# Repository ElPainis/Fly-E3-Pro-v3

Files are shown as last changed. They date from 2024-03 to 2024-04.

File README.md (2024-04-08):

${\small{\textcolor{darkgrey}{\texttt{Release: V1.22}}}}$

# ⚠️⚙️ Sovol SV06/+ Fly-E3-PRO-V3 conversion ⚙️⚠️

This repository contains guide for the hardwareconversion for the Fly-E3-PRO-V3 & Klipper firmware for the **Sovol SV06** 3D printer. I made this as a branch in collaboration with Bassamantor archive a better accessibility for the whole community. The hardware conversion described here should fit the SV06+ but is untested yet. Guide and Klipper Config for the is WIP SV06+. Alos check out [Bassamanators](https://github.com/bassamanator/Sovol-SV06-firmware/tree/master) GitHub.

| Printer | Branch |
| --- | --- |
| ${\normalsize{\textcolor{darkturquoise}{\texttt{Sovol SV06 Fly-E3-V3-Pro}}}}$ | ⚡ ${\small{\textcolor{darkturquoise}{\texttt{YOU ARE HERE}}}}$ ⚡ |
| Sovol SV06 | [master](https://github.com/bassamanator/Sovol-SV06-firmware/tree/master) |
| Sovol SV06 Skr-Mini-E3-V3.0 | [skr-mini-e3-v3](https://github.com/bassamanator/Sovol-SV06-firmware/tree/skr-mini-e3-v3) |
| Sovol SV06 Plus | [sv06-plus](https://github.com/bassamanator/Sovol-SV06-firmware/tree/sv06-plus) |
| All other printers | [any-printer](https://github.com/bassamanator/Sovol-SV06-firmware/tree/any-printer) |

**A short preview about what can you expect:**

(not realtime, speedup for better overview)



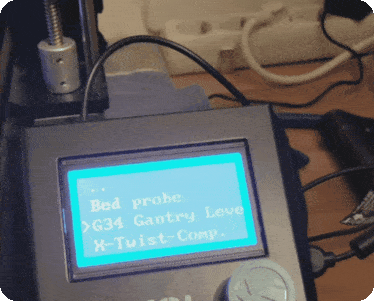
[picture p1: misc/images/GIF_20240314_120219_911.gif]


I am creating these files for my personal use and cannot be held responsible for what it might do to your printer. Use at your own risk.

## Outline
- [Contribution](#contribution)
- [Preface](#preface)
- [Disclaimer](#Disclaimer)
- [Features](#features)
- [Stay Up-to-Date](#stay-up-to-date)
- [Hardware Conversion](#Hardware-Conversion)
  - [BOM](#BOM)
  - [Step 1 - Electrical wiring](#Step-1---Electrical-wiring)
  - [Step 2 - Disassemble the mobo-box and ribbon-cable](#Step-2---Disassemble-the-mobo-box-and-ribbon-cable)
  - [Step 3 - Modifing Extruder Ribbon-Cable](#Step-3---Modifing-Extruder-ribbon-Cable)
  - [Step 4 - Modifing Mobo enclosure](#Step-4---Modifing-Mobo-enclosure)
  - [Step 5 - Stepper wiring](#Step-5---stepper-wiring)
  - [Step 6 - Assembly](#Step-6---assembly)
  - [Step 7 - Optional Neopixel](#Step-7---Optional-Neopixel)
  - [Hardware conversion sources](#hardware-conversion-sources)
- [Klipper Installation](#klipper-installation)
  - [Before You Begin](#before-you-begin)
  - [Flash Firmware](#flash-firmware)
  - [Download OSS Klipper Configuration](#download-oss-klipper-configuration)
- [Initial Steps](#initial-steps)
  1. [Adjust Configuration with MCU Path](#adjust-configuration-with-mcu-path)
  2. [Configure Your Printer](#configure-your-printer)
- [Adjust Your Slicer](#adjust-your-slicer)
- [Support Me](#support-me)
- [Directory Structure](#directory-structure)
- [FAQ](#faq)
- [Useful Resources](#useful-resources)
- [Sovol Official Links](#sovol-official-links)
- [Sources](#sources)

## Contribution
:heart:I want to thank [Bassamanator](https://github.com/bassamanator/Sovol-SV06-firmware/tree/sv06) for sharing his Klipper-Config and giving me advice for the whole project. Further I thank [Jan Oerter](https://www.youtube.com/user/MegaMuelleimer/) and [Dominik Schmidt](https://www.youtube.com/@dr.klipper) for their Anycubic i3 Mega conversion that inspired me for this project. Please check out [their GitHub](https://github.com/Schmelzerboy/I3-Mega-Klipper&ved=2ahUKEwj_2fKx-8qEAxW__7sIHc9iDd8QFnoECBUQAQ&usg=AOvVaw2BVSSPE56Auy_gCTLLL8iX) as well. Last but not least I thank the big maker community for advice, troubleshooting and sharing awesome creations. Beeing part of a community give us a feeling of wholesome and connected. Without you and the regardless help this project wouldnt be possible. Youre breathtaking! :heart:

## Preface

This Mod includes minor manipulation of the provided hardware. If this mod doesnt work out for you, its reversable in majority. You have to live with some minor cosmetic changes of the mainboard enclosure.

Preassumtion is you have crimping and solder tools and know how to use them. Many helpful sources are provided here like :tv:**vidoes** :tv: and 🖼️**pictures**🖼️ to make the job easier. Keep in mind youre the only one that can be hold responsible if things go wrong.

Requirements:
- screw drivers
- soldering iron & flux
- crimptool for insulated Terminals
- shrink Tubes
- dupon Connectors
- heatgun
- pliers to cut and to Grab
- wire stripper
- helping hand
- small file(s)
- zipties

Everything in this guide aims for easy accessibility. Despite it the prerequisite for this guide is youre familiar with Klipper. This conversion is recommend advanced users which are familiar with handling electronics and used Klipper at least once before.

> [!CAUTION]
> ## DISCLAIMER:
> 🔥⚡💀⚡🔥
>
> The conversion needs modification of the PSU wiring. This contains the potential risk of damaging your machine, firehazard or worst threading your life. If you unshure how to do proceed stop right away and get help! Don't improvise at something that can potentialy threading your life when done improper! When turning on the machine first time after conversion I recommend having a fire extinguisher to hand for the worst case. If issues occoure leave feedback by opening an issue. Read the complete guide with full attention. I can not be hold accountable for any damage or injuries. Youre doing this at your own risk.
> 
> 🚨 some basic safety rules for electrical DIY 🚨:
> 1. Turn Off the machine and unplug the Power
> 2. Make shure it cant be plugged in or turned on again accidantial.
> 3. Don't be lazy but smart. Unplug and disassemble the parts you want to modify as far as possible to get them on a table.
> 4. Use proper tools.

## Features
- Harware:
  - Z-Tilt & Gantry Level to further improve parallel alignment to printbed.
  - silent Hotend-Fan while printer is idling. Optional PWM!
  - dedicated driver cooling fan. Optional PWM!
  - Optional: Neopixel with preconfigured effects for your printhead for better view and status feedback. 🔴🟢🔵 Full customization via `neopixel.cfg`
     - This Mod requieres a already installed mod for partcooling! Like [these](https://www.printables.com/de/model/685826-high-flow-ducts-for-sv06-single-and-double-5015-pa)
- Klipper:
   - This is basically provided by awesome Bassamanator. I only did minor changes to the `printer.cgf` to make it work with the Fly E3 Pro V3. Only the greatest masters are getting copyied, so credit goes to Bassamanator!
   - 💥 This Klipper configuration is an _endpoint_, meaning that it contains **everything** that you could possibly need in order to have an excellent Klipper experience! 💥
   - Minimum configuration settings for `Mainsail` and `Fluidd`.
   - Macros:
     - **Improved** mechanical gantry calibration/`G34` macro that provides the user audio feedback, and time to check the calibration.
     - Misc macros: `PRINT_START`, `CANCEL_PRINT`, `PRINT_END`, `PAUSE`, `RESUME`.
     - Parking macros (parks the printhead at various locations): `PARKFRONT`, `PARKFRONTLOW`, `PARKREAR`, `PARKCENTER`, `PARKBED`.
     - Load/unload filament macros.
     - `PURGE_LINE` macro.
     - `TEST_SPEED` macro. Find instructions [here](#how-do-i-use-the-test_speed-macro).
     - Custom Diplay Menu
     - Klipper Adaptive Meshing & Purging (KAMP) integrated. Read about it [here](#how-do-i-enable-kamp-klipper-adaptive-meshing--purging).

[🔼 Back to top](#outline)

## Stay Up-to-Date

${\normalsize{\textcolor{goldenrod}{\texttt{Star ⭐ this project.}}}}$

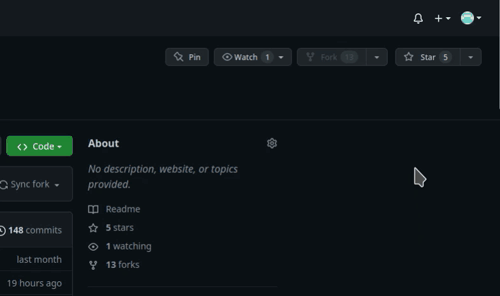
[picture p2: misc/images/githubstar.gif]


Watch for [updates]

[🔼 Back to top](#outline)

## Hardware Conversion
## BOM

This BOM is meant to give you an overview and some recommendation what is needed. Some parts are essential,  some can be done by DIY. Some there are a few parts with prequesitions. I marked them with the following pattern:
- basic requirement: :heavy_check_mark:
- can be done by DIY: ⚙️
- has prequesition: :large_blue_diamond:
- not necessary for the conversion, optional: :small_orange_diamond:

> [!CAUTION]
> ⚡ If you like to improvise: Dont improvise on the wiring. Use at least a diameter of AWG14 or 2,0mm². Thinner cables lead to a non reliable voltage supply for to mobo with may unexpected behavior or worse. ⚡

| Essential | Needed for Step  | Part Name | Price | Source |
| ----- | ----- | ---- | ----- | --- |
| :heavy_check_mark: | (6) Assembly  | Fly-E3-Pro-V3 | ~40 Money  | [AliExpress](https://a.aliexpress.com/_EwY8p5L) |
| :heavy_check_mark: | (1) Electrical wiring | 200cm each AWG14 Red & Black  | ~4 Money  | [AliExpress](https://a.aliexpress.com/_ExgydLn)  |
| :heavy_check_mark: | (1) Electrical wiring  | Cable Lug 3xSV2-4 & 3xSV2-5 | ~5 Money  | [AliExpress](https://a.aliexpress.com/_Exw61D7)  |
| :heavy_check_mark: | (1) Electrical wiring | MR60 Connector | ~6 Money  | [AliExpress](https://a.aliexpress.com/_EzVy9PX)  |
| :heavy_check_mark: | (1) Electrical wiring | Wire sleeve (8mm ID) | ~1 Money  | [AliExpress](https://a.aliexpress.com/_EJrBNvF)  |
| :heavy_check_mark: | (1) Electrical wiring  | Zipties 3.6mm width | ~2 Money  | [AliExpress](https://de.aliexpress.com/item/1005004666948984.html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)  |
| :heavy_check_mark: | (1) Electrical wiring | Zipties 2.5mm width | ~2 Money  | [AliExpress](https://de.aliexpress.com/item/1005004666948984.html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)  |
| :small_orange_diamond: | (3) Modifing Extruder Ribbon-Cable | Mainboard Ribbon Cable | ~ 12 Money | [Sovol](https://www.sovol3d.com/products/sovol-sv06-adapter-board-pcb-breakout-module-adapter-board-mainboard-ribbon-cable)|
| ⚙️ | (3) Modifing Extruder Ribbon-Cable | 2x JST XH 2,54 2pins | ~ 1 Money | [AliExpress](https://de.aliexpress.com/item/32954418743.html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)|
| ⚙️ | (3) Modifing Extruder Ribbon-Cable | 1x 5pin Female Dupont with wires | ~ 3 Money | [AliExpress](https://de.aliexpress.com/item/1005003638697583.html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)|
| :small_orange_diamond: | (3) Modifing Extruder Ribbon-Cable | Alternative to Dupont wires | ~ 20 Money | [Local Amazon](https://www.amazon.de/dp/B0CLD7S5VC/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)|
| ⚙️ |(6) Assembly| 50cm Stepper Wire | ~1 Money |[AliExpress]( https://a.aliexpress.com/_EHGpQVX) |
| ⚙️ |(6) Assembly| 80cm Stepper Wire | ~1 Money |[AliExpress]( https://a.aliexpress.com/_EHGpQVX) |
| :large_blue_diamond: :small_orange_diamond: |(7) Optional Neopixel| 4*1 Bit Neopixel | ~5 Money |[AliExpress](https://de.aliexpress.com/item/32962174474.html) |
| ⚙️ :large_blue_diamond: :small_orange_diamond: | (7) Optional Neopixel | 1x JST XH 2,54 3pins | ~ 1 Money | [AliExpress](https://de.aliexpress.com/item/32954418743.html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)|
| :heavy_check_mark: |Motivation| At least seven cookies or bits of sweets and a cup of hot drink 🍪🍬 | Depents on your taste |Anywhere |

## Step 1 - Electrical wiring
Requirements:
- AWG 14 wires
- MR60 Connector
- cable Lugs
- pliers
- wirestripper
- soldering iron
- crimping tool

> [!NOTE]
> This is the Part for the PSU-wiring to MOBO. You need to cut the wires and the sleeve in lenght, solder it with the connector and crimp the cable lugs.
> You may find this :tv:[video](https://youtu.be/w0pMjZ-rFQA?si=jAx5m2BBQhHhFl7G):tv: helpful for soldering and this :tv:[additional video](https://www.youtube.com/watch?v=GrwDEiFtXIc):tv: for applying the sleeve.

Procedure:
1. Use the pliers to cut the the materials in the length provided by this table:

| Quantity | Color  | Lenght | Needed for | 
| ----- | ----- | ---- | ----- |
| 2x | Red wire | 510 +/-10mm | connector to mobo |
| 1x | Black wire | 510 +/-10mm | connector to mobo |
| 2x | Red wire | 150 +/-5mm | PSU to connector |
| 1x | Black wire | 150 +/-5mm | PSU to connector |
| 1x | Protective sleeve | 470 +/-10mm | connector to mobo |
| 1x | Protective sleeve | 100 +/-10mm | PSU to connector |

> [!NOTE]
> The longer cables will be called CTM (connector to mobo), the short cables PSUC (PSU to connector) mind the 🖼️[electrical wiring diagram](#electrical-wiring-diagram)🖼️ to get an image of what you're about to archive.

2. Solder PSUC

Strip one end and solder all three 150mm wires it into the male connector. Use the helping hand to hold it in place. Round is for ground. A proper electrical connection is crucial as this connector is very likley to heat up and melt when there is a bad solderjoint. Apply the click-on insulation after inspecting the solder joint.

3. Solder CTM

Repeat the process with the three 510mm wires. Use the female connector.

4. Apply sleeve

Apply the sleeve to both wires and add a heatshrink to secure the sleeve and wires in place.

5. Crimping PSUC

Strip 6mm on the one end left and crimp the SV2-5(Bigger Fork) on all three cables. 

6. Crimping CTM

Repeat the process on the 510mm wires mentioned at 5. Use the SV2-4(smaller Fork)this time.

The result should look like this:
### Electrical wireing diagram
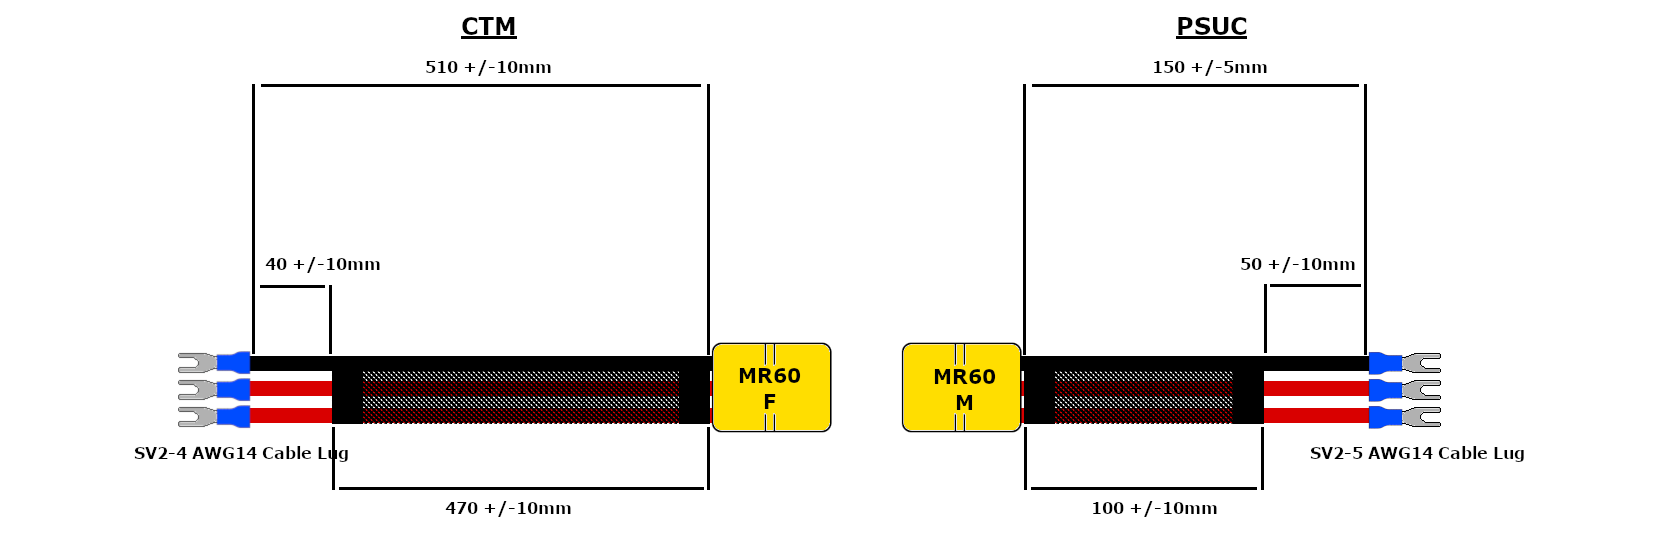
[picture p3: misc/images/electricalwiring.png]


🍪🍬 DONE. Time for a cup of hot drink and a cookie or a sweet. 🍪🍬

[🔼 Back to top](#outline)
## Step 2 - Disassembly

Requirements:
- Pliers
- screwdriver with hexhead

> [!NOTE]
> In this step all electronical parts are gonna disassembled from the printers frame as preparation for following modifications. The motherboard enclosure, stepper cables, ribbon-cable and the motherboard from the enclosure.
> You will may find this :tv:[video](https://www.youtube.com/live/SQ4Nzgl77F8?si=rxNRZa5gnDLFytx2&t=866):tv: till timestamp 22:05 useful. Mind the 🖼️[Sovol SV06 Pinout](#sovol-sv06-pinout)🖼️.

Procedure:
1. Turn off the machine and unplug power!
2. open the enclosure.
3. unscrew the power supply terminals.
4. unscrew the hot bed terminals. 
5. unplug the hot bed thermistor.
6. unplug all stepper motor cables.
7. unplug 'touch screen'
8. cut and remove the zipties in the two bottom outlets that hold the cables **be careful not to cut a wire accidently.**
9. gently remove all wires from the bottom outlets.
    1. Stepper motor cables
    2. Hot bed
10. unplug the ribbon-cable from the extruder-pcb
    1. unplug Nozzle thermistor.
    2. unscrew the nozzle 24V terminals.
    3. unscrew the normal fan 24V terminals.
    4. unplug the controllable fan.
11. close the enclosure and hold it closed. Then unlock mobo-enclosure and remove the enclosure with the ribbon cable from the printers frame.
12. place the motherboard enclosure on a flat surface and open it again to proceed. 
13. cut the ziptie that hold the extruder-ribbon-cable, **Carefully again not to cut a wire accidently.**
14. disassemble the ribbon-cable from the mobo and the enclosure.
15. unscrew the four motherboard screws. Store the motherboard somewhere. If your conversion is successful you wount need it anymore. Keep the screws!
15. back to the printer the Y-motor-cable and dual-Z-motor-cable are taped together. Gently peel of the tape so they're seperated after.
16. remove the Dual-Z-stepper-cable and store it somewhere. If the conversion is sucessful you wount need it anymore.

### Sovol SV06 Pinout


🍪🍬 DONE. Time for a cup of hot drink and a cookie or a sweet. 🍪🍬

[🔼 Back to top](#outline)

## Step 3 - Modifing Extruder Ribbon-Cable

Requirements:
- Wirestripper
- Soldering iron
- flux
- helping hand
- multimeter
- pliers
- tape for marking

> [!NOTE]
> Modification of the toolhead ribbon cable is neccessary so it fits all the connectors on the Fly-E3-V3-Pro. 🖼️[Schematic 1](#schematic-1)🖼️ down below shows the original toolhead ribbon cable. 🖼️[Schematic 2](#schematic-2)🖼️ shows the final product after modification.

> [!TIP]
> If you having the spare toolhead laying around go and get it. It will be very helpful for this step. A spare toolhead pcb comes really handy as you can easily check if your wiring is as intended.

### schematic 1:


(click for lager picture)

### schematic 2:
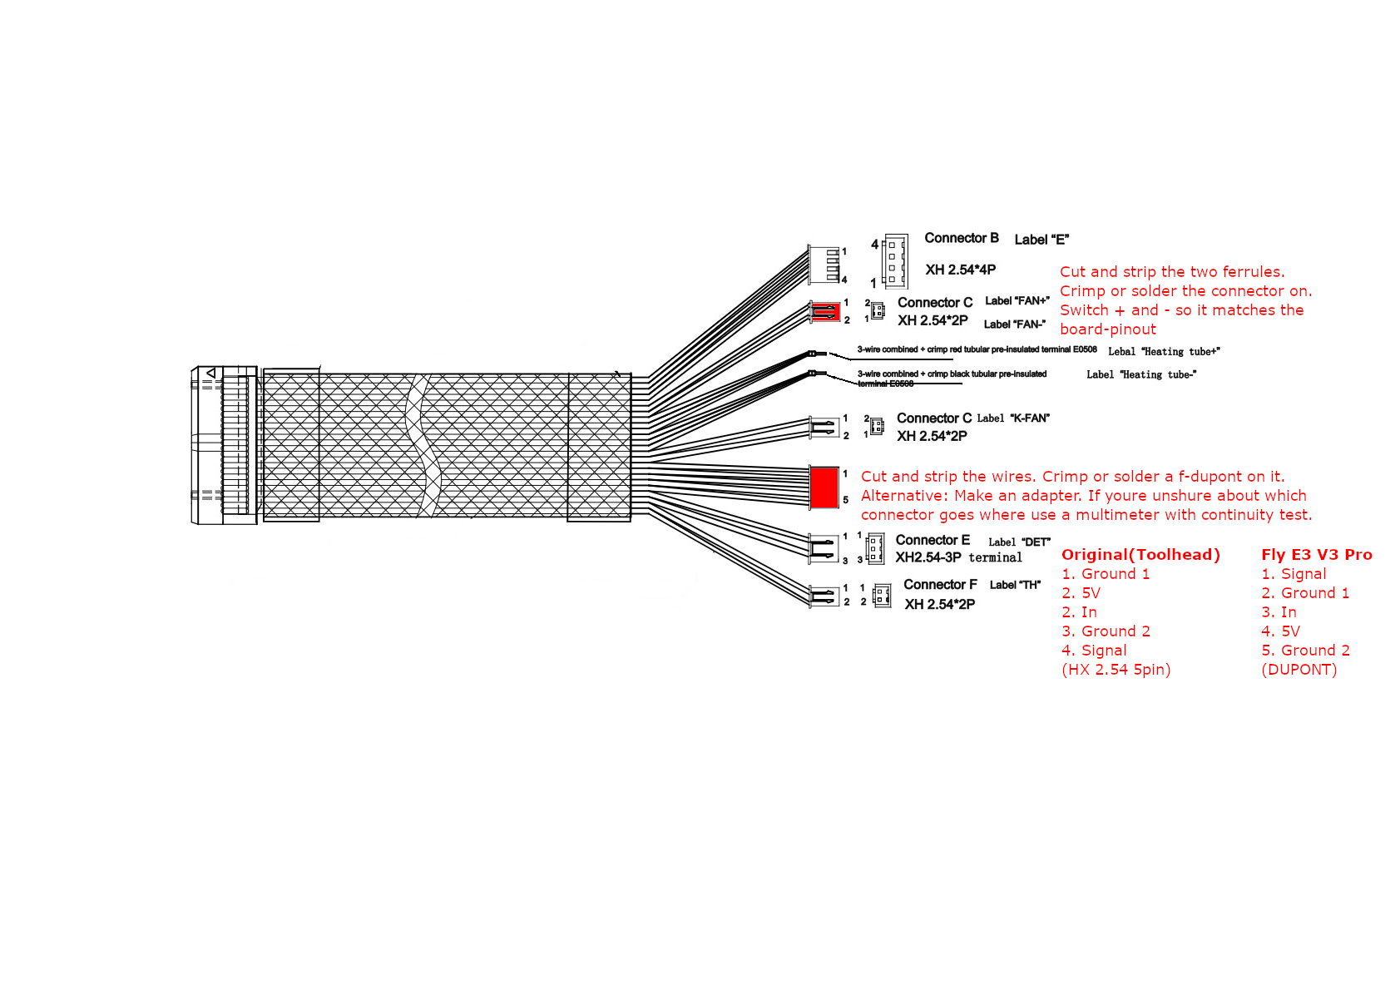
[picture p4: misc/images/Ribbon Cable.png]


(click for lager picture)

Procedure:
1. mark the cables for the probe with a tape so its easier to convert it. Mind the 🖼️[probe cable pinout](#probe-cable-pinout)🖼️.
2. cut the probe connector behind your marks cables and strip ~3mm.
3. cut the fan-ferrules from fan+ and fan- and strip ~3mm.
4. crimp or solder on the Dupont connector on the stripped probe-cables. Mind the 🖼️[probe cable pinout](#probe-cable-pinout)🖼️.
5. crimp or solder on JST-Connector on the stripped fan-cables.
6. check the polarity of the FAN. Mind the 🖼️[board pinout](#board-pinout)🖼️.
7. check the polarity of the K-FAN. Mind the 🖼️[board pinout](#board-pinout)🖼️.
8. check the pinout of the new probe-dupont-connector if it matches the Fly-E3-V3-pro. Mind the 🖼️[board pinout](#board-pinout)🖼️.
9. switch port 1 and 3 of the DET-Connector using the pliers.
10. (Optional) remove the tape marks from the probe-connector.

> [!TIP]
> Its possible to leave out the soldering or crimping job with the probe connetor by getting one of [these](https://www.amazon.de/dp/B0CLD7S5VC/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) and make an adapter. Its not really necessary and more costly, but maybe this is a more convinient option for you.

### Probe cable pinout

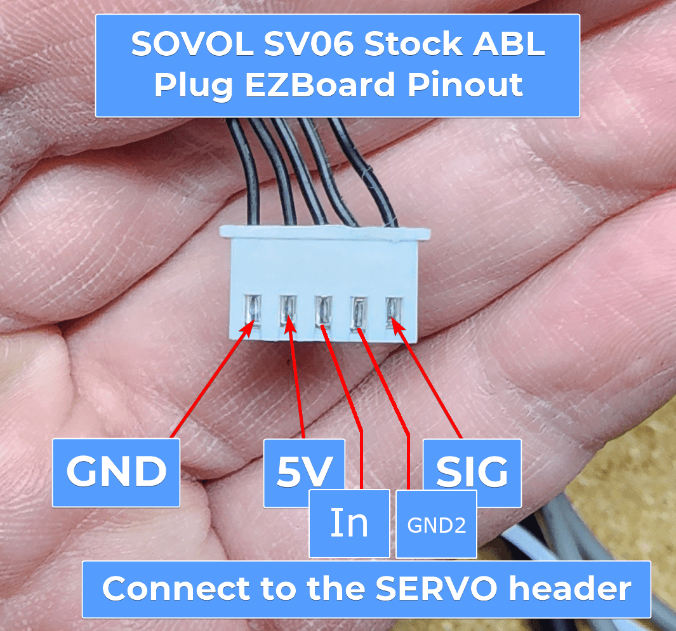
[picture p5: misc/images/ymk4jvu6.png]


### Board pinout
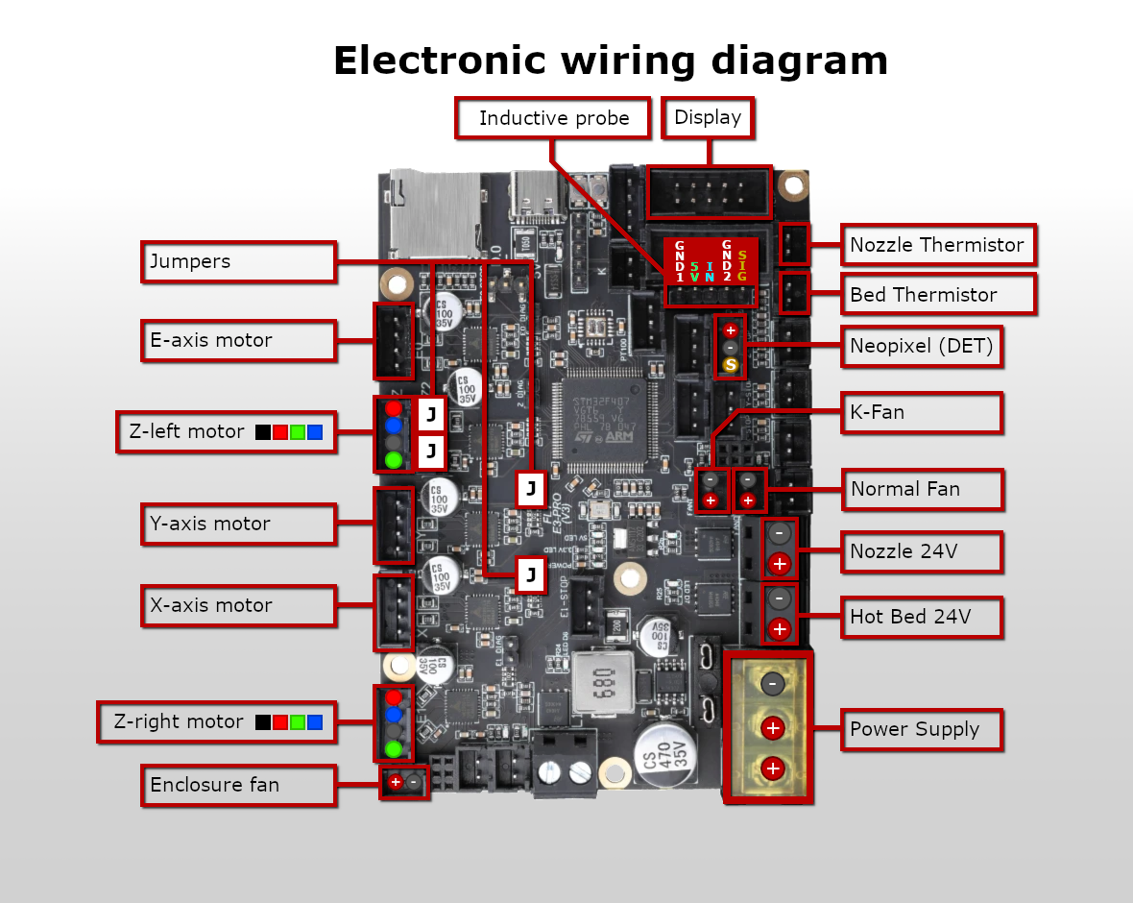
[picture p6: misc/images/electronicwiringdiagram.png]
 

> [!CAUTION]
> I strongly recommend to check wiring with the multimeter and the toolhead pcb if everything is wired up correctly before calling this done.

🍪🍬 DONE. Time for a cup of hot drink and a cookie or a sweet. 🍪🍬

[🔼 Back to top](#outline)

## Step 4 - Modifing Mobo enclosure
Requirements:
- pliers
- small file - For myself I did it with a nail file
- paper towels

> [!NOTE]
> The moobo-enclosure needs minor modification so it fits the Fly-E3-V3-Pro. Mind the 🖼️[enclosure sanding visualization](#enclosure-sanding-visualization)🖼️.

Procedure:
1. Cut the ribs with the pliers marked red in the picture. We need to do that to make room for the Wifi-Antenna at the backside of the board.
2. Sand the holes with the file ~1 up 2mm wider so the USB-connector and SD-Card-slot fit of the Fly-Mobo fit.
3. Test if the Fly mobo fits into the enclosure. If not check for for connectors especially the SD-slot as it stand out alot. A few tries may required to get it right.
4. When the board fits nice and snuggely into the enclosure remove it again clean the enclosure with water and dry it with paper towels.

### Enclosure sanding visualization
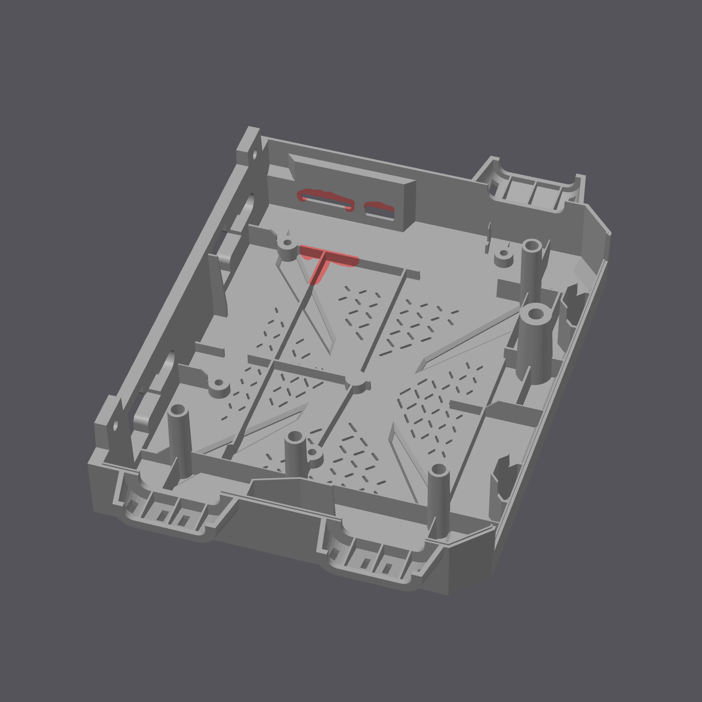
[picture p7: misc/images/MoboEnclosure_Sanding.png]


🍪🍬 DONE. Time for a cup of hot drink and a cookie or a sweet. 🍪🍬

[🔼 Back to top](#outline)

## Step 5 - Stepper wiring
Requirements:
- pliers

> [!NOTE]
> The two new stepper motor cables need modification for correct wiring.

Procedure:
1. check the 4-pin-connector for orientation for both Z motor cables on the Fly-E3-Pro-V3. Mind the [Z-Motor cable chart](#z-motor-cable-chart).
2. use the pliers to remoove the pins on the motherboard connector. You can pinch on the pins with moderate force, they wount break. Bend the little nose up again befor inserting them back in their connector-housing. Mind the left sequence shown in the table below.
3. check the 6-pin connector for orientation of both cables on Z-steppers.
4. use the pliers to get the right orientation on stepper connector. Bend the little plastic-holders gently upwarts and remove the pins. **Dont try to push the pins, you will break them!**. Bend the nose back again before inserting them in their connector-housing. Mind the right sequence shown in the table below.

### Z-Motor cable chart
| ⚪ Motherboard (up to down)  | ⬜ Stepper (left to right) | 
| ----- | ---- |
| 🔴 | ⬛🟥🟩🟦 |
| 🔵 | |
| ⚫ | |
| 🟢 | |

The result should look like this after final assembly:

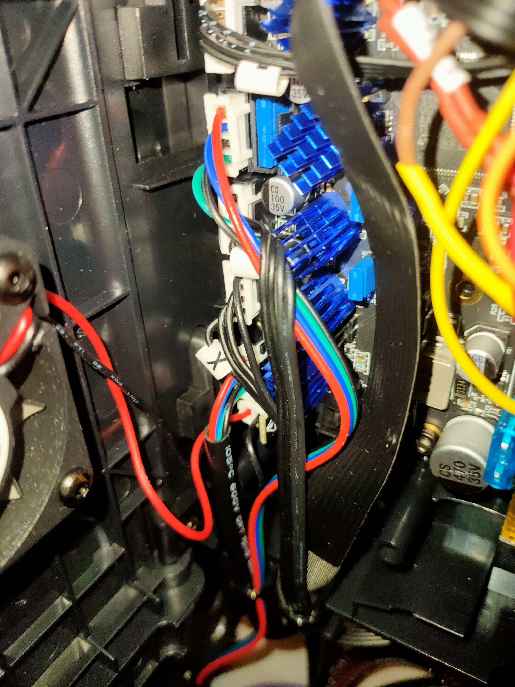
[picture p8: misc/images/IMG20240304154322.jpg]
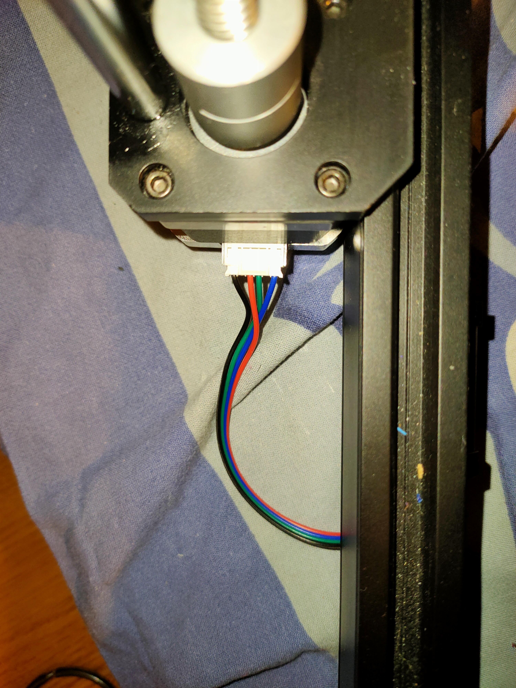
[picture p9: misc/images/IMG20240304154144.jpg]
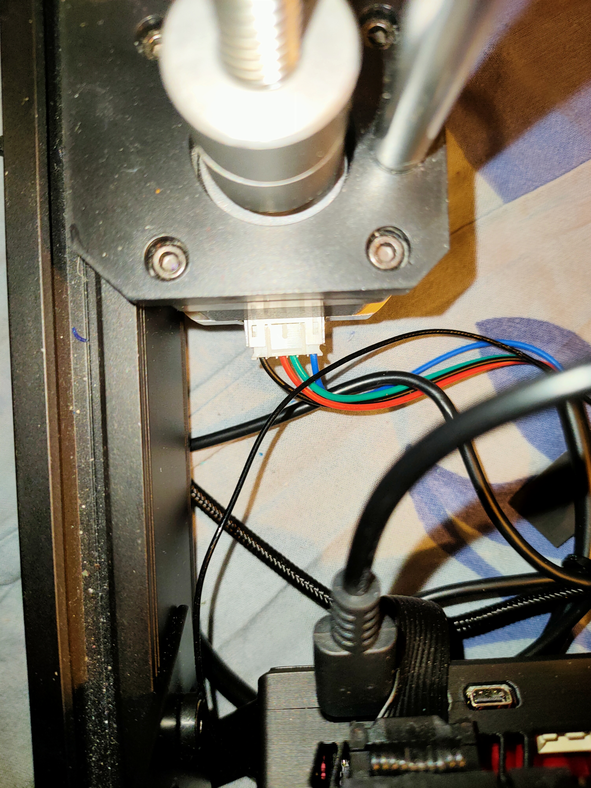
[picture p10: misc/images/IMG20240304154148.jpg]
  

🍪🍬 DONE. Time for a cup of hot drink and a cookie or a sweet. 🍪🍬

[🔼 Back to top](#outline)

## Step 6 - Assembly
Requirements:
- pliers
- zipties
- screwdriver with hex-head

> [!NOTE]
> Put everything together in reverse oder of dissasembly and check if the board is turning on after.

Procedure:
1. placing the motherboard
   1. place the jumpers and the fuse on the Fly-E3-V3-Pro if you havent already.
   2. place the heatsinks on all drivers.
   3. get the Fly-E3-V3-Pro and screw it into the motherboard enclosure using the four screws we saved from the disassembly.
2. electrical wiring 🖼️[mind the electronic wiring diagram](#electronic-wiring-diagram)🖼️
   1. get the cable we prepared earlier at [Step1](#Step-1---Electrical-wiring) and screw down the the lug connectors in the board. Terminal 3 is for ground. The other two are for voltage.
   2. Route the Power power cable we just screw in down in the opening. Dont ziptie yet!
3. Install ribbon cable 🖼️[mind the electronic wiring diagram](#electronic-wiring-diagram)🖼️
   1. get the modified ribbon cable and place it in the upper opening of the enclosure. Secure it with a ziptie.
   2. plug in all the cables from the extruder ribbon cable.

>[!IMPORTANT]
> Mind the orientation of the modified sensor-dupont-connector! Mind the wiring diagram down below to get everything right. Close it after with the screw.

4. assemble enclosure
   1. place the enclosure at the printers-frame and lock it in place.
   2. screw in the bed power cables and the thermistor.
   3. Route the power cable in place. Its much more stiff now so its now bigger bend radius as we crossing your bed-cable. Dont worry it isnt an issue. Secure the two cables with a ziptie.

>[!IMPORTANT]
> Mind the picture below to get an idea what is mentioned here.

5. stepper wiring 🖼️[mind the electronic wiring diagram](#electronic-wiring-diagram)🖼️
   1. plug in the 20cm stepper motor cable at Z.
   2. plug in the Y stepper motor cable at Y.
   3. plug in the X stepper motor cable at X.
   4. plug in the 80cm stepper motor cable at E1 for the right stepper.
   5. route all the cables through the hole and secure them with a ziptie.

>[!IMPORTANT]
> test if the motherboard-enclosure is closing properly. If not check for conflicts with the cables. **DONT TRY TO FORCE IT CLOSE, IT WILL BREAK!**

6. frame cable routing. Mind the 🖼️[frame visualization](#frame-visualization) for substep i till vii 🖼️ and the Mind the [Z-Motor cable chart](#z-motor-cable-chart) for substep iii and viii.
   1. route the Y-stepper cable, the 80 cm stepper-motor-cable and the power cable underneath the Y-stepper. Secure them with a ziptie.
   2. route the 20cm stepper motor cable underneath the left 2040 extrusion. Remove the plastic cover. Route the cable inside the left extrusion and click in the cover over back on to secure it.
   3. plug the 20cm stepper motor cable into the left stepper motor.
   4. Remove the plastic extrusion cover under the right 2040 extrusion.
   5. lift the frame at the right back corner and losen the glued foot on the right back corner by twisting it with moderate force. Do not remove completly!
   6. route the 80cm stepper motor underneath the foot and press it back on. 
   7. route the 80cm cable further to the motor and click in the plastic cover to secure it.
   8. Plug the cable into the right motor.

>[!IMPORTANT]
> check if everything is well routed. Move the bed slowly back and forth and sense if there is any resistance. Also check for any other potential collisions with the rerouted cables. If everything seems well proceed. If not check the uncutted zipties if theyre the source of the issues.

7. PSU wiring
> [!NOTE] 
> You may find this :tv:[video](https://youtu.be/YTUfaLn1awc?si=KQ4-fF_gmnzqi0rD&t=149):tv: till timestamp 3:47 helpful

   1. disassemble the psu by release the two M4 bolts from the frame. 
   2. disassemble the PSU-cover from PSU.
   3. release the two screws in the PSU terminal holding the the cable lugs.
   4. remove the whole now loose cable with the connector.
   5. screw in the short cable you made at step 1. Mind the polarity on the PSU. **Double check a mistake May fry your board!** 🖼️[Mind the electronic wiring diagram](#electronic-wiring-diagram)🖼️.
   6. assembple back psu-cover and route the cable with connector trough the hole provided by the cover.
   7. screw the psu back on the printers frame.
8. Final steps
   1. connect the MR60-connector so the board is provided with power.
   2. check if the psu is turned off and then plug in the power supply.
   3. turn on the power supply. **🔥🧯 A fire extinguisher nearby is recommend. 🧯🔥**
   4. Check if the boards led's and the led of the probe lights up. When nothing is 💥burning/exploding🔥 or smell♨️ weird after 1 minute then everything seems to be fine.
   5. Cut all installed zipties so they dont infere with anything. Mind the 🖼️[frame visualization](#frame-visualization).
   6. close the mainboard enclosure and secure it with the screw.

### electronic wiring diagram


### frame visualization
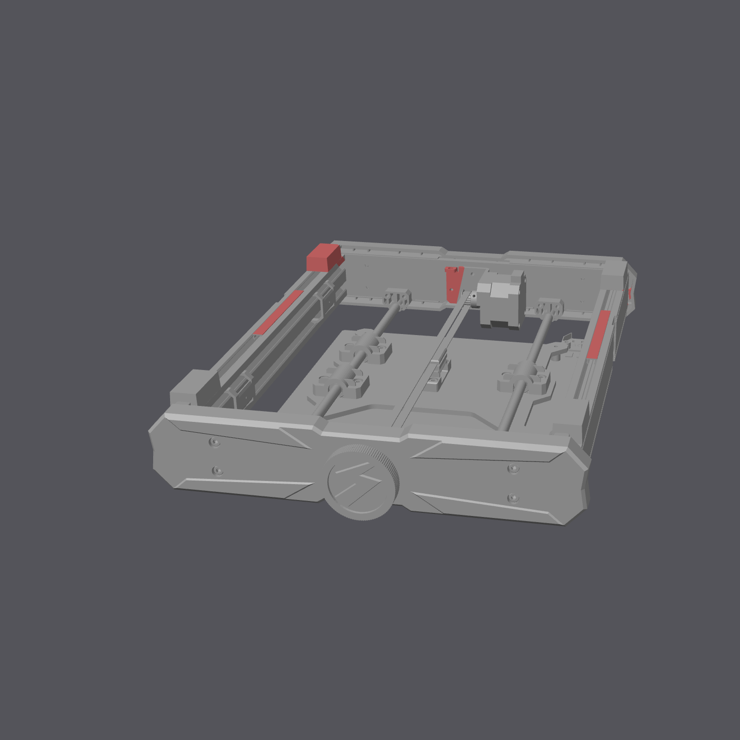
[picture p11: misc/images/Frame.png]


🥳 Congrats your conversion seems to be successfull at this point 🥳
🍪🍬 DONE. Time for a cup of hot drink and a bunch of cookies or sweets. 🍪🍬

[🔼 Back to top](#outline)

##  Step 7 - Optional Neopixel
Requirements:
- printed LED-holder (STL is in Folder 'misc/STL')
- helping Hand
- flux
- Solder iron
- 4*1 Bit Neopixel
- Superglue
- 1x JST XH 2,54 3pins with (pre)crimped connectors and 115 +/- 5mm AWG28 wire
- wirestripper
- pliers
- Two M3*6 screws (its possible to use the ones that holded the original partcooler)

> [!NOTE]
> We are going to solder the wires in the Mini-Neopixel, glue it on the holder and then install it.

> [!IMPORTANT]
> to fullfil this step soldering skills beyond beginners level are required. It's assumed you had practiced at least a few times soldering and did simple solderjobs on PCB's.

 Print Settings:
 - 0.4 Nozzle
 - 0.1mm layerheight
- Solid infill
- Heat resistant material like PETG or ABS
- Place on Buildplate as in the STL

1. Preperation
   1. strip around 2mm of the three AWG 28 wires connected to the JST-header. 
   2. place the Neopixel in the helping hand, clamp it down.
2. Soldering
   1. apply flux on the three pads on the backside and apply tin on the pads with the soldering iron. Go short and hot around 400°C. Very little is enough.
   2. place the prepared cables with the connector over the three soldered pads. Take your time to bring them in position. Clamp them with the helping hand very close over the pads. Its a little fiddly but you make it!
   4. When the cables are in position apply some flux again over the cables and solder them on the pretinned pads. I recommend starting with DIN and work your way to GND. ***Go in very short and hot or may the insulation will start to melt.** 🟡=In 🔴=5V ⚫=GND
   6. check for shorts. If everything seems fine lay it nearby and proceed.
3. Installation on holder
   1. route the cables in the grove with the pliers and gently press the PCB down till everything fits. Its a fiddly job again. If there is alot resistance when pressing the PCB down lift it again and route the cables with the pliers. When everything is right the PCB should go in with a slight click.
   3. Inspect if the pcb sits firmly in the LED-Bracket. When everything seems good, lift it again and apply a drop of superglue on the left and right side of the Neopixel-PCB. Press it on with moderate force for 30 seconds and let it set for ~2 hours.
   4. While the glue is setting you can route the cables through the routing-groove using the pliers.
   5. when the glue is settled screw the holder into the two provided holes for the former partcooler and connect the neopixel to the printhead PCB. Mind the correct wiring, switch if necessary using the pliers to lift the small platic noses. I the cable is a little too long you can route it behind the PCB and then plug the connector in. Mind the 🖼️[Hotend PCB pinout @ P7](#Hotend-PCB-pinout) so your JST-connector should go  🔴=V ⚫=G 🟡=S
   6. secure the cable with a small ziptie on the probes cable so it cant touch the heater block.
4. Testing
   1. See 8 at [setup Klipper](#Configure-Your-printer-and-initial-setup).

The result should look like:

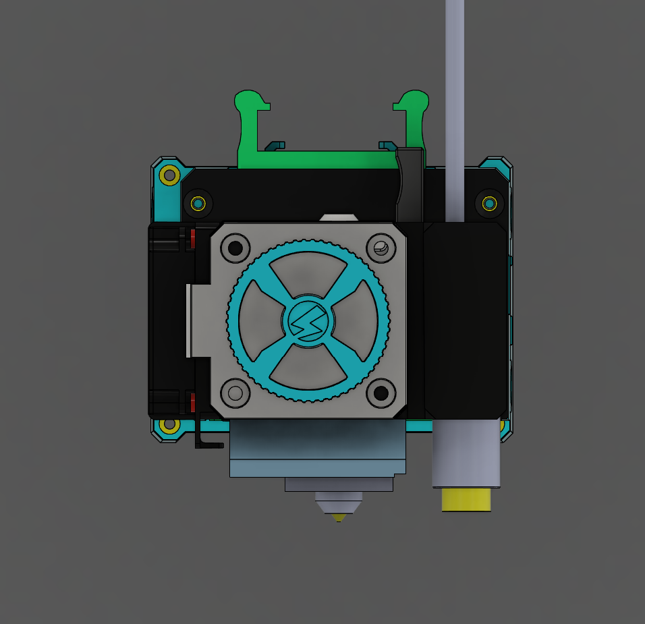
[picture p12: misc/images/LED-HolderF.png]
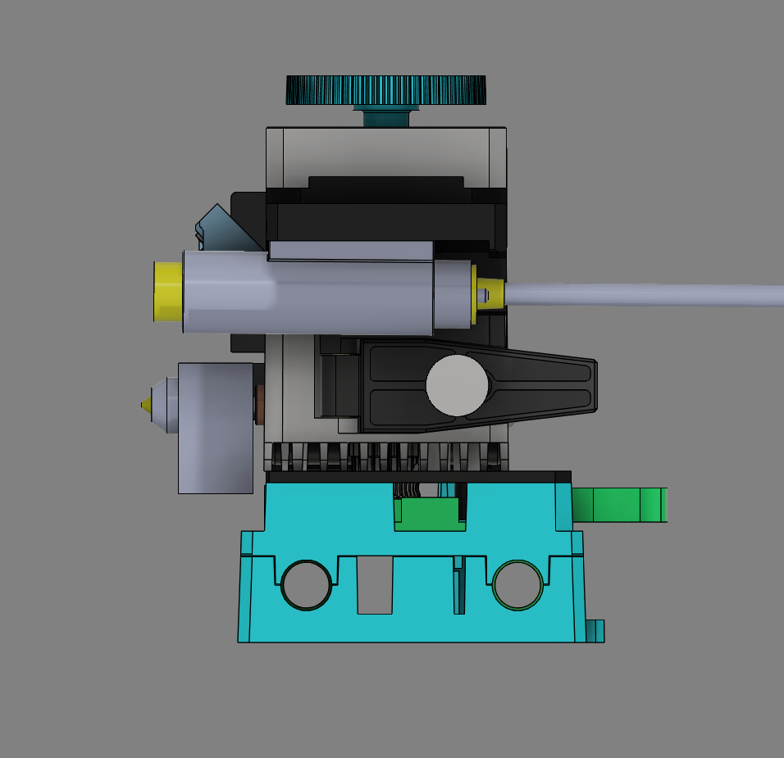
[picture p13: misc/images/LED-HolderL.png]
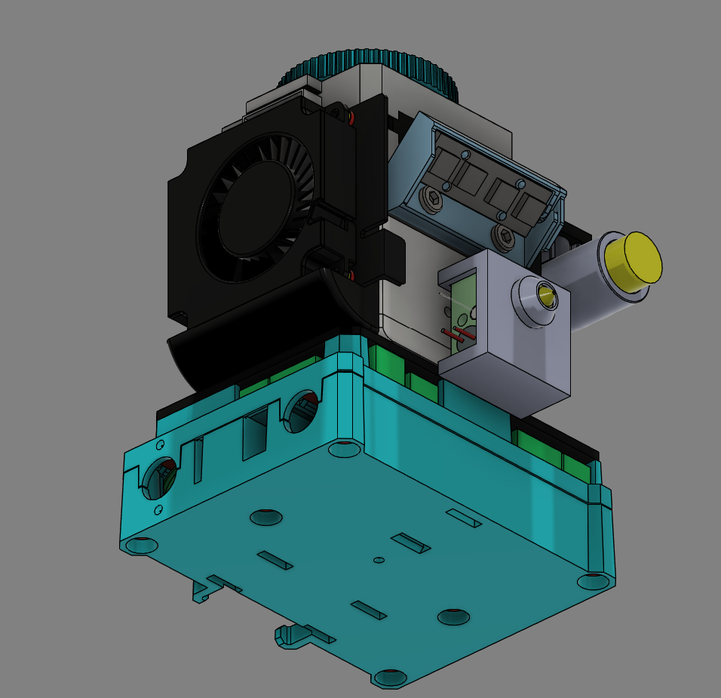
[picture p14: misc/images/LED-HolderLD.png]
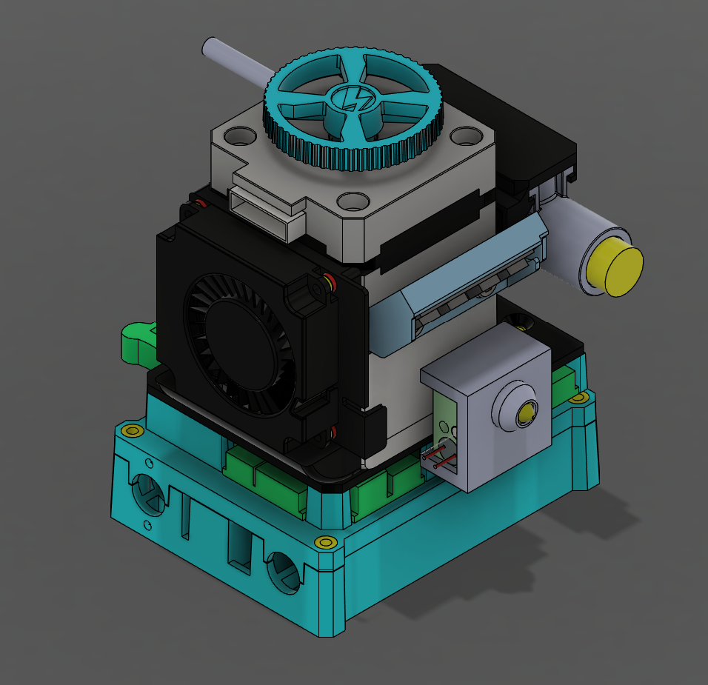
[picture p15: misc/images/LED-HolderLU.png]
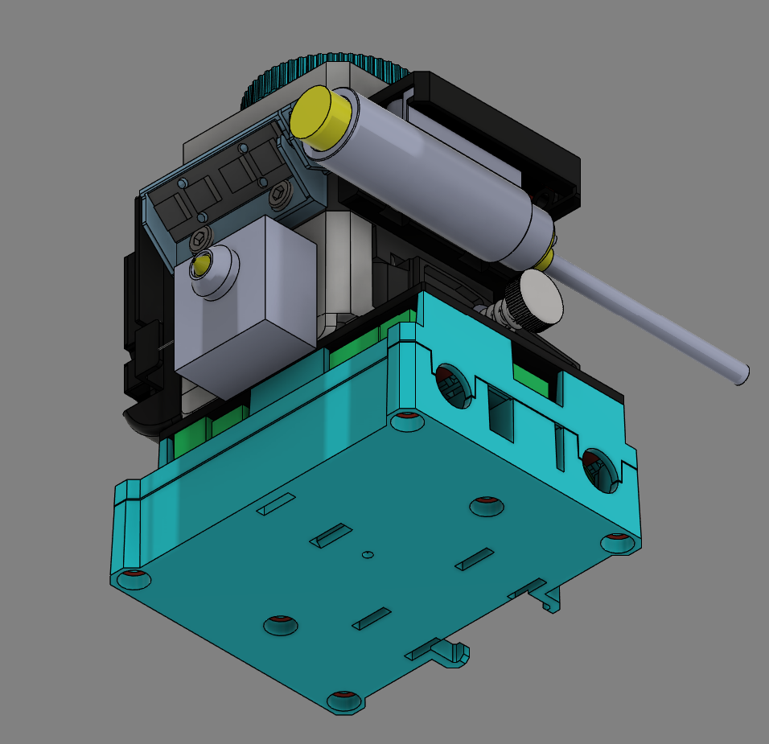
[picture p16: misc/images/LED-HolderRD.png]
    

**For a 3D-visualization check on [this](./misc/stl/ExtruderLEDHolderAssembly.stl).**

### Hotend PCB pinout



🆒 Congrats you added RGB, quality of live and level of coolness improved 😎

[🔼 Back to top](#outline)

## Hardware conversion sources
- [Bassamanator](https://github.com/bassamanator/everything-sovol-sv06)
- [Blakadder](https://sv06.blakadder.com/Parts/electronic-parts/)
- [TeamGloomy](https://teamgloomy.github.io/fly_e3_pro_v3_general.html)
- [th3dstudio](https://support.th3dstudio.com/helpcenter/ezboard-v2-sovol-sv06-stock-abl-sensor-wiring/)

# Klipper Installation
## Before You Begin

- This entire page is a **9 minute read**. Save yourself _hours of troubleshooting_ and read this documentation fully.
- ⚠️ Make sure your printer is in good physical condition, because print and travel speeds will be _a lot faster_. Beginners would be wise to run through [these steps](https://github.com/bassamanator/everything-sovol-sv06/blob/main/initialsteps.md).
- ⚠️ [Disable](https://github.com/bassamanator/everything-sovol-sv06/blob/main/howto.md#disable-usb-cable-5v-pin) the USB cable's 5V pin.
- Follow the steps in order. If an error was reported at a step, do no proceed to the next step.
- It is assumed that you are connected to your host Raspberry Pi (or other host device) via SSH, and that your printer motherboard is connected to the host via a data USB cable. 💡 Most of the micro USB cables that you find at home are _unlikely_ to be data cables, and it is not possible to tell just by looking.
- It is also assumed that the username on the host device is `pi`. If that is not the case, edit `moonraker.conf` and `cfgs/misc-macros.cfg` to change any mentions of `/home/pi` to `/home/yourUserName`.
- Klipper _must_ be installed on the host beforehand. Easiest is to use [MainsailOS](https://github.com/mainsail-crew/mainsail/releases/latest). [KIAUH](https://github.com/th33xitus/kiauh) is another option.
- Klipper _must_ be up to date.
  - In `Fluidd`, you can do this from `Settings` > `Software Updates`.
  - In `Mainsail`, you can do this from `Machine` > `Update Manager`.
- Robert Redford's performance in _Spy Game (2001)_ was superb!
- It is assumed that there is one instance of Klipper installed. If that is not the case, the steps in this guide will not work _perfectly_ for you.
- Your question has probably been answered already, but if it hasn't, please post in the [Discussion](https://github.com/bassamanator/Sovol-SV06-firmware/discussions) section.
- I would recommend searching for the word `NOTE` in this configuration. There are roughly half a dozen short points amongst the various files that you should be aware of.
<!-- - Link to recommended parts. -->

### Important Note About Stepper Motor Current

For the Fly-E3-Pro-V3.0, the run_current for x, y, z stepper motors has been reduced in the printer.cfg, because the standard current seems to make the steppers dangerously hot. You may have to increase the current, or if the motors are still too hot, you may have to decrease it.

💡 Although stepper motors can withstand upwards of 125C, they should at the most get hot to the touch (~55C), not very hot.

[🔼 Back to top](#outline)

## Optinal Compile Firmware
Its recommended using the `firmware.bin`from the `misc/` folder. But ist possible to compile the firmware by yourself. Use the following settings:

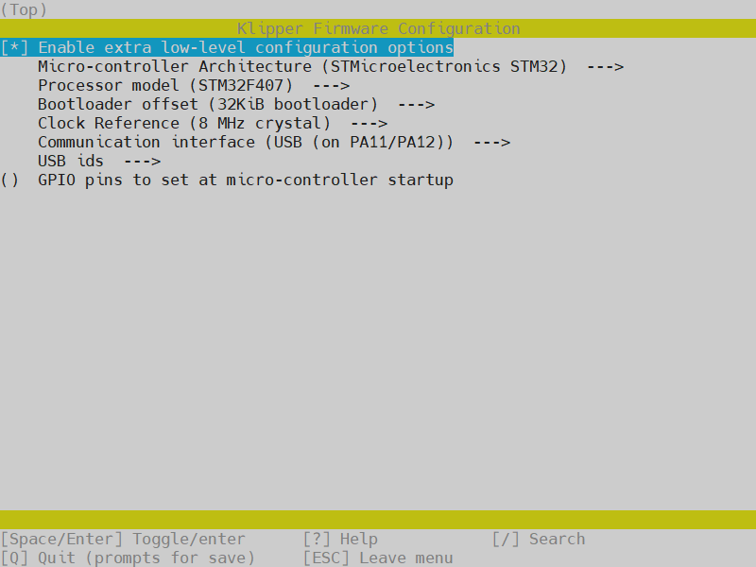
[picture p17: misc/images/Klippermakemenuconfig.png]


## Flash Firmware
💡 If you flashed Klipper onto your motherboard in the past, you can skip this step.

Please note:

- For the sake of simplicity, I will refer to the klipper firmware file as `firmware.bin` even though the actual filename is something along the lines of `firmware-v0.12.0-10-gea2f6bc0-UNTESTED.bin`.
- The firmware file **must** be named `firmware.bin`.
- The firmware file is located in `misc/`.
- ⚠️ Many users have reported having issues flashing Klipper using the Sovol microSD card.

#### 1. Prepare the microSD Card for Flashing with These Parameters

- Size: `16GB` maximum.
- File system: `FAT32`.
- Allocation unit size: `4096 bytes`.
- Must not contain any files _except_ the firmware file.

#### 2. Flashing Procedure
##### Method 1 - Basic
1. Disconnect any USB cables that might be connected to the motherboard.
2. Copy `firmware.bin` to the microSD card. The firmware is located in the directory `misc`.
3. Make sure the printer is off.
4. Insert the microSD card into printer.
5. Turn on the printer and wait a minute (usually takes 10 seconds).
6. Turn off the printer and remove the microSD.

##### Method 2 - Advanced
I recommend using [Katapult](https://github.com/Arksine/katapult). As it's a topic on its very own, it wount explained on this repo how to use it. It's **not necessary** but a quality of live upgrade as you dont have to use SD-Cards anymore, once you set it up. It comes really handy when Klipper-Updates need an update of the firmeware. You can easily flash firmeware via the SSH-Console not even touching the MOBO or printer.

>[!TIP]
> Mind the follow changes in firmeware compilation:
> Bootloader offset (32KiB bootloader)  --->
> USB ids  --->

⏲️ At this point, it's not possible to tell with certainty whether your flash was successful. You can check at your desktop-PC if the file was renamed to `firmware.cur` on the SD-card which is an indicator for a successfull flash. Anyways continue on with the guide.

[🔼 Back to top](#outline)

## Download OSS Klipper Configuration
### Method 1: Clone the Repository

💡 Make sure git is installed (sudo apt update && sudo apt install git).

1. `cd ~/printer_data/config`
2. Empty entire ~/printer_data/config folder.
- In linux, you can delete files via rm fileName and directories via rmdir directoryName.
- In linux, you can list files and folders via ls -lah.
3. `git clone -b master --single-branch https://github.com/ElPainis/Fly-E3-Pro-v3.git .` ⚠️ Don't miss the period!

### Method 2: Download the ZIP

1. [Download](https://github.com/ElPainis/Fly-E3-Pro-v3/archive/refs/heads/fly-e3-pro-v3.zip) the `ZIP` file containing the Klipper configuration.
2. See `Step 2` in `Method 1`.
3. The parent folder in the `ZIP` is Sovol-SV06-firmware-master. This is relevant in the next step.
4. Extract only the contents of the parent folder into `~/printer_data/config.`

[🔼 Back to top](#outline)

## Initial Steps

## Adjust Configuration with MCU Path

💡 Make sure the host and printer are connected via USB.

1. Find what port the `mcu` (printer motherboard) is connected to via _one_ of the following commands:

   - `ls /dev/serial/by-id/*`
   - `ls /dev/serial/by-path/*`

   1. The output will be something along the lines of
      - `/dev/serial/by-id/usb-1a86_USB2.0-Serial-if00-port0`

2. Adjust the `[mcu]` section in `printer.cfg` accordingly.

   ```yaml
   # 📝 This is just an example
   [mcu]
   serial: /dev/serial/by-id/usb-1a86_USB2.0-Serial-if00-port0
   restart_method: command
   ```

3. Do a `FIRMWARE_RESTART`.

If the Klipper flash that you did earlier was successful, and you've done everything else correctly, you should see no errors or warnings in the `Mainsail`/`Fluidd` dashboard. 🎉 **Your printer has been Klipperized!** 🎉

[🔼 Back to top](#outline)

## Configure Your Printer and initial setup

❗☠️ **Your finger should be on the power switch for most of these steps** ☠️❗

❗☠️ **Power off if there is a collision/problem** ☠️❗

💡 The ${\small{\textcolor{red}{\texttt{EMERGENCY STOP}}}}$ button in your dashboard works faster than hitting the power switch.

💡 Do a practice emergency stop.

💡 I recommend no filament be loaded for any of these steps.

💡 Check if you get correct temperature reading from the bed and hotend. It should correspond with your roomtemperature.

💡 Check if your hotend and bed heats up when you enter a number at the temperatures setting.

💡 Check if the hotend fan and partcooler fan are working. First one should start as you start heating the hotend, the second one you can activate via `Mainsail`/`Fluidd`.

📝 You will be pasting/typing these commands into the `Mainsail`/`Fluidd` console.

1. Check to see if `X` and `Y` max positions can be reached, and adjust `position_max`, if necessary. You might be able to go further, which is great, but I recommend leaving a 2mm gap for safety.
   1. `G28`
   2. `G90`
   3. `G1 X223 F3000`
   4. `G1 Y223 F3000`
2. Do a mechanical gantry calibration; `G34`. After the controlled collision against the beam at the top, there will be a 10 second pause for you to verify that both sides of the gantry are pressed up against the `stoppers` at the top. You will hear a succession of beeps.
   1. Figure out your `Z` `position_max` by baby stepping your way up to the beam, and adjust `position_max`, if necessary.
   2. OPTIONAL: Now you can use Z-Tilt
3. PID tune the bed. Ideally, all PID tuning should occur at the temperatures that you print most at.
   1. `PID_TEST_BED TEMP=70`
   2. `SAVE_CONFIG` (once completed)
4. PID tune the extruder while part cooling fan runs at 25%.
   1. `PID_TEST_HOTEND TEMP=245`
   2. `SAVE_CONFIG` (once completed)
5. Calibrate X-Twist-Compensation. Make sure your nozzle if very clean. Follow the wizard and do the [Paper test](https://www.klipper3d.org/Bed_Level.html?h=probe_calibrate#the-paper-test).
   1. `AXIS_TWIST_COMPENSATION_CALIBRATE ` 
   2. Follow `AXIS_TWIST_COMPENSATION_CALIBRATE` setup in `Mainsail`/`Fluidd`.
6. Adjust `z_offset`. Make sure your nozzle if very clean. Do the [Paper test](https://www.klipper3d.org/Bed_Level.html?h=probe_calibrate#the-paper-test).
   1. `DO_PROBE_CALIBRATE`
   2. Follow `z_offset` setup in `Mainsail`/`Fluidd`.
   3. `SAVE_CONFIG` (once completed)
7. Create a bed mesh.
   1. `DO_CREATE_MESH`
   2. `SAVE_CONFIG` (once completed)
8. Test Neopixel
   1. If your Neopixel is turning on after Klipper booted its a good sign
   2. type in in your console `LED_Printing`. Your Neopixel should turn to bright white.

>[!IMPORTANT]
> For future calibration after initial setup of your printer use:
> 1. `mechanical gantry calibration`
> 2. `screw tilt calculate` (if you have the required modifications)
> 3. `Z-Tilt` to archieve the best first layer possible.

>[!NOTE]
> You will need `mechanical calibration` to enshure your X-gantry squarness. After setting up your `AXIS_TWIST_COMPENSATION_CALIBRATE ` you can enshure getting the right readings for further calibration like `screw tilt calculate`. Only then you will fully benefit from `Z-Tilt`. After calibrating your machine like this you will need `Z-Tilt` from time to time. When you observe degenerations in bedmesh, like a tilted mesh and/or increasing in deviation its time for a `Z-Tilt`. If there is no improvment in the bed mesh at all try a `mechanical gantry calibration` first and a `Z-Tilt` after.

🏁 If you've made it here, then your Klipperized and modded printer is ready to print! 🏁

_But first_, adjust your slicer.

[🔼 Back to top](#outline)

## Adjust Your Slicer

📝 If you are using the slicer bundles found on this repo, you can skip this section.

### Start G-Code

It varies depending on your slicer. Find instructions [here](https://ellis3dp.com/Print-Tuning-Guide/articles/passing_slicer_variables.html#slicer-start-g-code).

## End G-Code

```
PRINT_END
```

## Line Purge

If you would like to print a purge line before your print starts, at the end of your start gcode, on a new line, add one of the following:

- `PURGE_LINE`; prints a standard purge line.
- `LINE_PURGE`; prints KAMP's purge line. ⚠️ Do not attempt to use without reading [this section](#how-do-i-enable-kamp-klipper-adaptive-meshing--purging).

```yaml
# 📝 This is just an example Start G-Code
PRINT_START ...
PURGE_LINE
```

[🔼 Back to top](#outline)

## Directory Structure

This repository contains many files and folders. Some are _necessary_ for this Klipper configuration to work, others are not.

- **Necessary** items are marked with a ✅.
- Items that can _optionally_ be deleted are marked with a 💠.
<!-- tree -a -C -I '.directory' -L 1 -F -->

```sh

├── CODE_OF_CONDUCT.md 💠
├── CONTRIBUTING.md 💠
├── .git/ ✅❔
├── .github/ 💠
├── .gitignore ✅❔
├── cfgs/ ✅
├── moonraker.conf ✅
├── osskc.cfg ✅
├── printer.cfg ✅
├── LICENSE 💠
├── misc/ 💠
├── README.md 💠
├── SECURITY.md 💠
└── .vscode/ 💠
```

[🔼 Back to top](#outline)

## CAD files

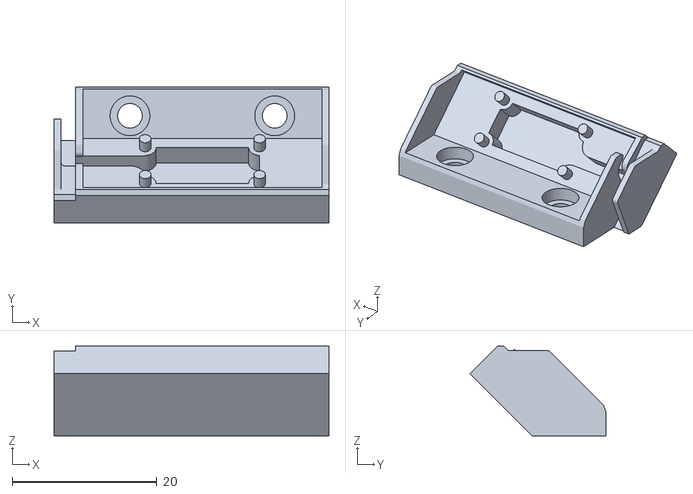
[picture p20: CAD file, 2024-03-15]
misc/stl/LEDHolder2.stl
38.0 x 18.8 x 12.4

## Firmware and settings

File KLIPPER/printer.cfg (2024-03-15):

#####################################################################
#    General Information & Contributions
#####################################################################

#    This file contains pin mappings for the Fly E3V3pro for Sovol SV06.
#    Inspiration for this project came by reading about this project. https://github.com/Schmelzerboy/I3-Mega-Klipper
#
#    I thank all makers that care for community and sharing ideas, revise code or simply gave answers to stupid questions.
#    
#    Most important: Pacific Rim is the very best Kaiju-Movie ever made! 
#
#    Contributions for this project:
#    Bassamanator - https://github.com/bassamanator/
#    Jan Oerter      (YT Schmelzerboy) - https://www.youtube.com/channel/UCTYNFDNzhLzgfR8x1OPZsGg
#    Dominik Schmidt (YT Dr. KLipper)  - https://www.youtube.com/@dr.klipper
#
#
## Default Compile Settings
#> CanBoot (https://github.com/Arksine/CanBoot)
#      Micro-controller Architecture (STMicroelectronics STM32)  --->
#      Processor model (STM32F407)  --->
#      Build CanBoot deployment application (32KiB bootloader)  --->
#      Clock Reference (8 MHz crystal)  --->
#      Communication interface (USB (on PA11/PA12))  --->
#      Application start offset (32KiB offset)  --->
#      USB ids  --->
#  ()  GPIO pins to set on bootloader entry
#  [*] Support bootloader entry on rapid double click of reset button
#  [ ] Enable bootloader entry on button (or gpio) state
#  [ ] Enable Status LED
#
#> Klipper 
#  [*] Enable extra low-level configuration options
#      Micro-controller Architecture (STMicroelectronics STM32)  --->
#      Processor model (STM32F407)  --->
#      Bootloader offset (32KiB bootloader)  --->
#      Clock Reference (8 MHz crystal)  --->
#      Communication interface (USB (on PA11/PA12))  --->
#      USB ids  --->
#  ()  GPIO pins to set at micro-controller startup
#
#####################################################################

#####################################################################
#    Include
#####################################################################
[include ./osskc.cfg]

#####################################################################
#    MCU Config
#####################################################################
[mcu]
# NOTE Obtain definition by "ls -l /dev/serial/by-path/" or "ls -l /dev/serial/by-id/"
serial: /dev/serial/by-id/usb-1a86_USB2.0-Serial-if00-port0
restart_method: command

## Uncomment this part if you use the Raspberry Pi MCU
# > https://www.klipper3d.org/RPi_microcontroller.html

[printer]
kinematics: cartesian
max_velocity: 200
max_accel: 3000
max_z_velocity: 15
max_z_accel: 45
square_corner_velocity: 5.0

#####################################################################
#    X/Y/Z Stepper Settings
#####################################################################

[stepper_x]
step_pin: PE3
dir_pin: PE2
enable_pin: !PE5
microsteps: 16
rotation_distance: 40
endstop_pin : tmc2209_stepper_x:virtual_endstop
position_endstop : 0
position_max: 223 # NOTE You can adjust this if you have more room
homing_speed: 40
homing_retract_dist: 0

[tmc2209 stepper_x]
uart_pin: PE4
run_current: 0.700
stealthchop_threshold: 0
interpolate: False
sense_resistor: 0.150
driver_SGTHRS: 81
diag_pin: PA2

[stepper_y]
step_pin: PB9
dir_pin: !PB8
enable_pin: !PE1
microsteps: 16
rotation_distance: 40
endstop_pin: tmc2209_stepper_y:virtual_endstop
position_endstop: 0
position_max: 223 # NOTE You can adjust this if you have more room
homing_speed: 40
homing_retract_dist: 0

[tmc2209 stepper_y]
uart_pin: PE0
run_current: 0.800
stealthchop_threshold: 0
interpolate: False
sense_resistor: 0.150
driver_SGTHRS: 81
diag_pin: PB10

[stepper_z]
step_pin: PA15
dir_pin : PD7
enable_pin: !PC2
microsteps: 16
rotation_distance: 4
endstop_pin: probe:z_virtual_endstop
position_min: -2
position_max: 248 # NOTE You can adjust this if you have more room
homing_speed: 5

[tmc2209 stepper_z]
uart_pin: PA8
run_current: 0.400
stealthchop_threshold: 0
interpolate: False
sense_resistor: 0.150
#diag_pin: PC4 # Should not be needed

[stepper_z1]
step_pin: PC13
dir_pin : PC0
enable_pin: !PC15
microsteps: 16
rotation_distance: 4
endstop_pin : probe:z_virtual_endstop

[tmc2209 stepper_z1]
uart_pin: PC14
run_current : 0.500
interpolate : False
driver_SGTHRS: 81
#diag_pin: PD1 # Should not be needed

#####################################################################
#    Extruder
#####################################################################

[extruder]
step_pin: PD4
dir_pin: PD3
enable_pin: !PD6
microsteps: 16
rotation_distance: 4.64 # NOTE Calibrate e-steps https://www.klipper3d.org/Rotation_Distance.html#calibrating-rotation_distance-on-extruders
nozzle_diameter: 0.400
filament_diameter: 1.750
heater_pin: PA5
sensor_type: ATC Semitec 104GT-2
pullup_resistor: 2200
sensor_pin: PA4
control: pid
pid_kd: 86.991
pid_kp: 21.479
pid_ki: 1.326
pressure_advance: 0.035
min_temp: 0
max_temp: 300
max_extrude_only_distance: 150.0
min_extrude_temp: 150
# max_extrude_cross_section: 5 # NOTE Uncomment this line if you intend on using KAMP pruge
min_extrude_temp   : 150

[tmc2209 extruder]
uart_pin: PD5
run_current: 0.550
stealthchop_threshold: 0
interpolate: False
sense_resistor: 0.150

#####################################################################
#    Bed Heater
#####################################################################

[heater_bed]
heater_pin: PA0
sensor_type: ATC Semitec 104GT-2
pullup_resistor: 2200
sensor_pin: PA3
#control: pid
#pid_kp: 64.440
#pid_ki: 0.773
#pid_kd: 1343.571
min_temp: 0
max_temp: 110

#####################################################################
#    Probe Related
#####################################################################

[probe]
pin	: ^PC5
#control_pin: PB0  
x_offset: 27
y_offset: -20
#z_offset: 0
samples: 3
samples_result: median
samples_tolerance: 0.01
samples_tolerance_retries: 5

[safe_z_home]
home_xy_position: 84.50, 135 #NOTE The probe is at the center of the bed.
speed: 100.0
z_hop: 10
z_hop_speed: 15

[bed_mesh]
speed: 175
mesh_min: 27, 6
mesh_max: 222, 203
probe_count: 5,5
algorithm: bicubic
fade_start: 1
fade_end: 10
fade_target: 0

#####################################################################
#    Fans
#####################################################################

[fan]  #Fan1
pin	: PA6
#cycle_time: 0.50

[controller_fan MCU_Fan]  #Fan2
pin	: PB6
#cycle_time: 0.50

[heater_fan E0]  #Fan0
pin	: PA7
#cycle_time:
heater: extruder
heater_temp: 50.0
fan_speed: 1.0

#[heater_fan E1]  #Fan3
#pin: PB7
##cycle_time:
#heater: extruder1
#heater_temp: 50.0
#fan_speed: 1.0

#####################################################################
#    Temperatures
#####################################################################

[temperature_sensor BTT_pi]
sensor_type: temperature_host
min_temp: 10
max_temp: 100

[temperature_sensor mcu_temp]
sensor_type: temperature_mcu
min_temp: 0
max_temp: 100

#####################################################################
#    X twist compensation
#####################################################################
#    This feature enables adjustment for axis twist for X-Axis:
#    https://www.klipper3d.org/Axis_Twist_Compensation.html

[axis_twist_compensation]
#speed: 50
#   The speed (in mm/s) of non-probing moves during the calibration.
#   The default is 50.
#horizontal_move_z: 5
#   The height (in mm) that the head should be commanded to move to
#   just prior to starting a probe operation. The default is 5.
calibrate_start_x: 27
calibrate_end_x: 196.75
calibrate_y: 135

#####################################################################
#    Z Tilt
#####################################################################
#    This feature enables independent adjustment of multiple z steppers to adjust for tilt:
#    https://www.klipper3d.org/Config_Reference.html#z_tilt

[z_tilt]
z_positions                :
                             -51,135
                             274,135   
points                     :
                             0,135
                             169.75,135
speed                      : 40
horizontal_move_z          : 10
retries                    : 5
retry_tolerance            : 0.02

#####################################################################
#    Bedscrew adjust
#####################################################################
#    nylock mod or silicone mod needed for this. Read more:
#    https://www.rearvuemirror.com/guides/nylock-mod-for-the-mk3s
#    https://www.printables.com/de/model/465809-jig-for-silicone-tube-leveling-jig-for-sovol-sv06-
#    https://github.com/bbbenji/PMSBLM

[bed_screws]
screw1_name: front left
screw1: 26.5, 31
screw2_name: front right
screw2: 196.75, 31
screw3_name: back right
screw3: 196.75, 201
screw4_name: back left
screw4: 26.5, 201
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

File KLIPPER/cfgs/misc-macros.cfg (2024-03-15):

[force_move]
enable_force_move: True

# NOTE If you're using a Raspberry Pi, you can uncomment the next 2 lines, optionally.
# [temperature_sensor raspberry_pi]
# sensor_type: temperature_host

# NOTE If you're using a an Orange Pi, you can uncomment the next 3 lines, optionally.
# [temperature_sensor Orange_Pi]
# sensor_type: temperature_host
# sensor_path: /sys/class/thermal/thermal_zone0/temp

[virtual_sdcard]
path: /home/biqu/printer_data/gcodes

# NOTE Cancel objects feature is enabled. If you're using a low powered device, comment out [exclude_object].
# Also see [file_manager] section in moonraker.conf.
[exclude_object]

[pause_resume]
[display_status]

[delayed_gcode DISABLEFILAMENTSENSOR]
initial_duration: 1
gcode:
    SET_FILAMENT_SENSOR SENSOR=filament_sensor ENABLE=0

[gcode_macro _globals]
variable_filament_sensor_enabled: 0 # NOTE Enable(1) or disable(0) the filament sensor, if one is connected
variable_beeping_enabled: 1 # NOTE Enable(1) or disable(0) beeping everywhere except during gantry calibration
variable_bed_temp_over: 10 # NOTE Start print if bed temperature is over by this amount, otherwise wait for temperature drop
variable_kamp_enable: 1 # NOTE Enable(1) or disable(0) KAMP (adaptive mesh)
variable_pre_purge_prime_length: 1.40
gcode:
    # Don't delete this section

[gcode_macro CONDITIONAL_BEEP]
gcode:
    # Parameters
    {% set i = params.I|default(1)|int %}           ; Iterations (number of times to beep).
    {% set dur = params.DUR|default(100)|int %}     ; Duration/wait of each beep in ms. Default 100ms.
    {% set freq = params.FREQ|default(2000)|int %}  ; Frequency in Hz. Default 2kHz.

    {% set BEEPING_ENABLED=printer["gcode_macro _globals"].beeping_enabled|default(-1)|int %}

    {% if BEEPING_ENABLED == 1 %}
        BEEP I={i} DUR={dur} FREQ={freq}
    {% endif %}

[gcode_macro ADJUST_FILAMENT_SENSOR_STATUS]
gcode:
    # Parameters
    {% set NEWSTATUS = params.ENABLE|default(-1)|int %}

    {% set FILAMENT_SENSOR_ENABLED=printer["gcode_macro _globals"].filament_sensor_enabled|default(-1)|int %}

    {% if FILAMENT_SENSOR_ENABLED == 1 and NEWSTATUS != -1 %}
        SET_FILAMENT_SENSOR SENSOR=filament_sensor ENABLE={NEWSTATUS}
    {% endif %}

[gcode_macro M109]
rename_existing: M99109
gcode:
    #Parameters
    {% set s = params.S|float %}
    
    M104 {% for p in params %}{'%s%s' % (p, params[p])}{% endfor %}  ; Set hotend temp
    {% if s != 0 %}
        TEMPERATURE_WAIT SENSOR=extruder MINIMUM={s} MAXIMUM={s+1}   ; Wait for hotend temp (within 1 degree)
    {% endif %}

[gcode_macro M190]
rename_existing: M99190
gcode:
    #Parameters
    {% set s = params.S|float %}

    M140 {% for p in params %}{'%s%s' % (p, params[p])}{% endfor %}   ; Set bed temp
    {% if s != 0 %}
        TEMPERATURE_WAIT SENSOR=heater_bed MINIMUM={s} MAXIMUM={s+1}  ; Wait for bed temp (within 1 degree)
    {% endif %}

[gcode_macro PURGE_LINE]
gcode:
    {% set PRE_PURGE_PRIME_LENGTH=printer["gcode_macro _globals"].pre_purge_prime_length|default(1.40)|float %}
    ADJUST_FILAMENT_SENSOR_STATUS ENABLE=1

    #   Misc variables
    {% set extrudeAmount = 26.6 %}
    {% set movementLength = 100.0 %}
    {% set movementSpeed = 15 * 60 %}
    {% set xStart = 0.5 %}
    {% set yStart = 0.5 %}

    #   Set safe speeds
    {% set maxVelocity = printer.configfile.settings.printer.max_velocity|default(200)|int %}
    {% set maxVelocityAdjusted =  (0.95 * maxVelocity * 60)|int  %}

    G92 E0.0                                ; reset extruder
    G90                                     ; Absolute positioning
    G0 X{xStart} Y{yStart} F{maxVelocityAdjusted}         ; move to purge position
    G1 Z0.4 F500.0                          ; move to purge height
    M83                                     ; Relative extrusion mode
    G1 E{PRE_PURGE_PRIME_LENGTH} F500       ; pre-purge prime LENGTH SHOULD MATCH YOUR PRINT_END RETRACT
    G1 X{xStart + movementLength} E{extrudeAmount} F{movementSpeed}       ; intro line 1

    G92 E0.0                                ; reset extruder
    M82                                     ; Absolute extrusion mode
    G1 Z5.0                                 ; move nozzle to prevent scratch

[gcode_macro CANCEL_PRINT]
rename_existing: BASE_CANCEL_PRINT
gcode:
    SET_IDLE_TIMEOUT TIMEOUT={printer.configfile.settings.idle_timeout.timeout} ; set timeout back to configured value
    CLEAR_PAUSE
    SDCARD_RESET_FILE
    PRINT_END
    BASE_CANCEL_PRINT

[gcode_macro PRINT_START]
gcode:
    ADJUST_FILAMENT_SENSOR_STATUS ENABLE=1
    # Parameters
    {% set bedtemp = params.BED|int %}
    {% set hotendtemp = params.HOTEND|int %}
    {% set chambertemp = params.CHAMBER|default(0)|int %}
    
    # Other variables
    {% set bedtempSlicer = bedtemp %}
    {% set bedtempOver = printer["gcode_macro _globals"].bed_temp_over|default(0)|int %}
    {% set maxVelocity = printer.configfile.settings.printer.max_velocity|default(200)|int %}
    {% set maxVelocityAdjusted =  (0.90 * maxVelocity * 60)|int %}
    {% set kampEnabled=printer["gcode_macro _globals"].kamp_enable|default(0)|int %}

    {% if printer.configfile.settings.safe_z_home %}
        {% set startX = printer.configfile.settings.safe_z_home.home_xy_position[0]|float %}
        {% set startY = printer.configfile.settings.safe_z_home.home_xy_position[1]|float %}
    {% endif %}

    {% set bedtempAlmost = ((bedtemp - 2, 0, printer.heater_bed.temperature|int)|max, bedtemp)|max %}
    {% set hotendtempStepOne = ((hotendtemp, printer[printer.toolhead.extruder].temperature|int)|min, 150)|max %}
    {% set hotendtempStepTwo = ((hotendtemp, printer[printer.toolhead.extruder].temperature|int)|min, 170)|max %}

    # If bed-temp-almost is higher than bed-temp by a maximum of bed-temp-over
    {% if bedtempAlmost > bedtemp %}
        {% if (bedtempAlmost - bedtempOver) <= bedtemp %}
            {% set bedtemp = bedtempAlmost %}
        {% endif %}
    {% endif %}
	LED_off                                              ; LED OFF
    G90                                                  ; absolute positioning
    M140 S{bedtempAlmost}                                ; set & don't wait for bed temp
    M104 S{hotendtempStepOne}                            ; set & don't wait for hotend temp
	LED_Homing                                           ; HOME LED
    G28 X Y
    {% if printer.configfile.settings.safe_z_home %}
        G1 X{startX} Y{startY} F{maxVelocityAdjusted}
    {% endif %}

    LED_Heating                                          ; LED HEATING
    M190 S{bedtempAlmost}                                ; set & wait for bed temp
    {% if kampEnabled == 0 %}
        M104 S{hotendtempStepTwo}                            ; set & don't wait for hotend temp
    {% endif %}
    M190 S{bedtemp}                                      ; set & wait for bed temp
    M140 S{bedtempSlicer}                                ; set & don't wait for bed temp ; set temp to sliced setting regardless
    LED_Homing                                           ; LED HOMING
    {% if kampEnabled == 0 %}
        BED_MESH_PROFILE LOAD=default                        ; NOTE if not using a mesh, comment out this line
        M104 S{hotendtemp}                                   ; set & don't wait for hotend temp
        G28 Z                                                ; final z homing
    {% else %}
        G28 Z                                                ; final z homing
        BED_MESH_CALIBRATE                                   ; KAMP mesh
        M104 S{hotendtemp}                                   ; set & don't wait for hotend temp
    {% endif %}

    G1 X0 Y0 F{maxVelocityAdjusted}
	LED_Heating                              ; LED HEATING
    M109 S{hotendtemp}                       ; set & wait for hotend temp
    G1 Z20 F3000                             ; move nozzle away from bed
	LED_Printing                             ; LED Printing
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

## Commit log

2024-03-21 Update README.md
    Edited Klipperinstallation.
2024-03-24 Update README.md
    Improvment in Klipper-Firmware-Download. Added folder 'KLIPPER' and ZIP-File
2024-03-26 Rearranged file directory Changes 'OSS Installation' for better user experience
    [Adaptive_Meshing.cfg, CALIBRATION.cfg, KAMP_Settings.cfg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]
2024-04-04 Major Update. Fixed countless typos. Description is reworked so its eaier to understand. Added wiring diagrams for clearer instructions. Added pictures and STL's for better visualizations.
2024-04-04 added ExtruderLEdHolderAssembly
2024-04-06 README.MD - Added the ribbon cable as optional. Reworked the whole table for better overview and accuracy in wording.
2024-04-06 Revert "README.MD - Added the ribbon cable as optional. Reworked the whole table for better overview and accuracy in wording."
    This reverts commit a1af45d160e7db13ff9ee7b0e50f463fe28ef741.
2024-04-06 README.MD - Reworked BOM description.
2024-04-08 Reworked electronic wiring diagram
2024-04-11 Fixed a missing wiring instruction in the electronic wiring diagram.
